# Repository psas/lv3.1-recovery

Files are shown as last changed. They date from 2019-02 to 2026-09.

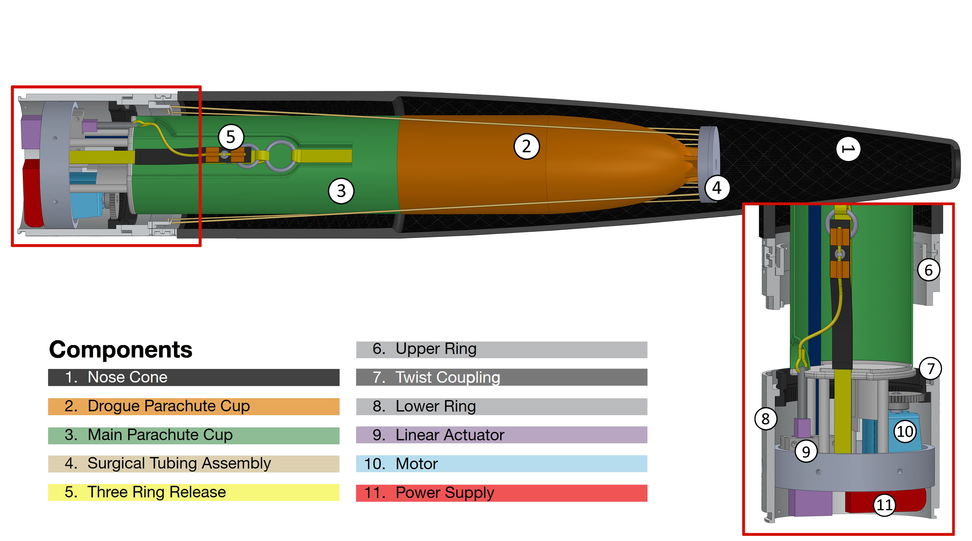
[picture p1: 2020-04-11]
images/stack_sideways.jpg

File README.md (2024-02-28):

# LV-3.1 Recovery Repository

The LV-3.1 Electromechanical Recovery System (ERS) is a fully-resettable recovery system for the [PSAS](http://psas.pdx.edu/) Launch Vehicle v 3.1 (LV-3.1). Each ERS "unit" releases a single parachute. The top unit deploys our ballute test parachute that's in the nose cone, the next ERS unit releases a standard drogue, and the final ERS unit releases the main parachute.

## Mechanical CAD
All mechanical CAD has been moved to OnShape and can be found [here](https://cad.onshape.com/documents/03e169a7501c9614bcd8fe34/w/d2206dc55680e29e4d8f6e15/e/43f9d4697ebc459acca1436a).

## Control System

In this Git repo is a PCB with STM32F091 microcontroller that controls the system. See the ControlSystem directory.

## Testing and Analysis

The ERS system will be tested by dropping it from a helicopter over a field. Many parameters must be considered for this test including wind speed, altitude, field size, parachute drag coefficients, and parachute release timing. Analysis of drop test dispersal patterns based on fixing some parameters and simulating variation in others enables us to choose an appropriate drop site and drop parameters. Analysis notebooks can by found in the /analysis directory.

* [Parent Directory](https://github.com/psas/lv3.1-recovery/tree/master/Analysis)
* [Primary mission analysis document](https://github.com/psas/lv3.1-recovery/blob/master/Analysis/Mission_Analysis.ipynb)
* [Jupyter Notebook to run simulations](https://github.com/psas/lv3.1-recovery/blob/master/Analysis/drop_test_simulator.ipynb)

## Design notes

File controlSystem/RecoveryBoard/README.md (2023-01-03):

# Electromechanical Recovery System (ERS) v4.0 Controller Board 

## General information
This board controls the ERS v4 modules in LV3.1 and hopefully eventually in LV4.

Full documentation can be found [here](https://docs.google.com/document/d/1TOoC-d3vpsw2uvtvazEmFV9_g59nFPVRWKC9Ye5qgKw/edit?usp=sharing)

## Firmware

The firmware is written in C and runs on top of ChibiOS, a small RTOS. See the "firmware" directory. The [oresat-firmware](https://github.com/oresat/oresat-firmware) repository has instructions on how to get started on the tool chain.

## License

All materials in this repo are copyright Portland State Aerospace Society and are licensed under the CERN Open Hardware Licence Version 2 -
Strongly Reciprocal (CERN-OHL-S v2), or any later version. A copy of the license is located in [here](LICENSE.md).

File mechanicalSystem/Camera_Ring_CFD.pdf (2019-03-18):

### Analysis of Drag Created by Portland State Aerospace Society’s Camera Ring Module and its Impact on Theoretical Maximum Achievable Altitudes Using Computational Fluid Dynamics in STAR CCM+

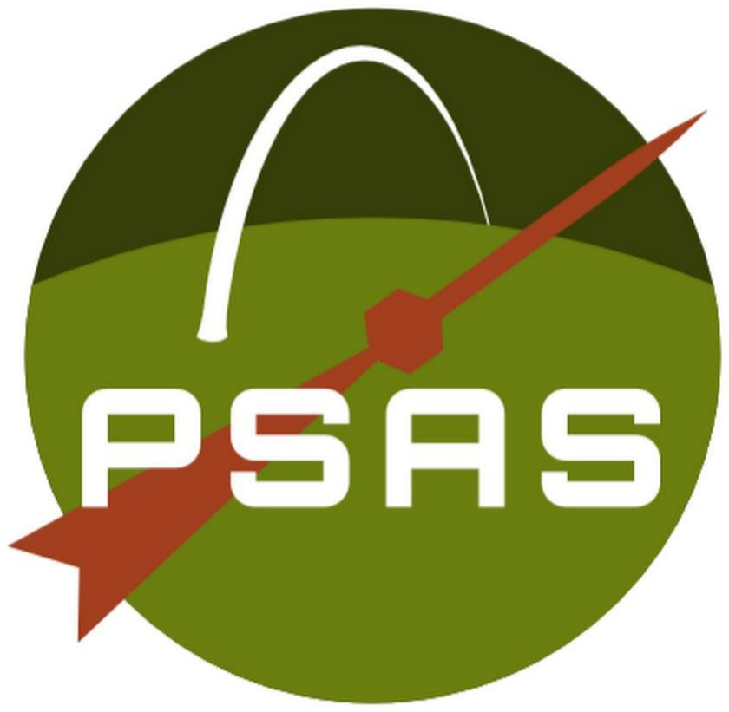
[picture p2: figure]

### 18 March 2019

### Grady Goodenough

### ME 448 Final Report

Overview

The Portland State Aerospace Society (PSAS) is constantly striving to add new improvements and features to their rockets, commonly referred to as launch vehicles, to further their reach both literally and figuratively. One of the latest components to fly aboard PSAS’ last launch vehicle, LV3, was a module comprised of 6 small cameras with wide fields of view, as shown in Figure 1. This enabled post processing of the footage into a 360° view of the launch and recovery of LV3.

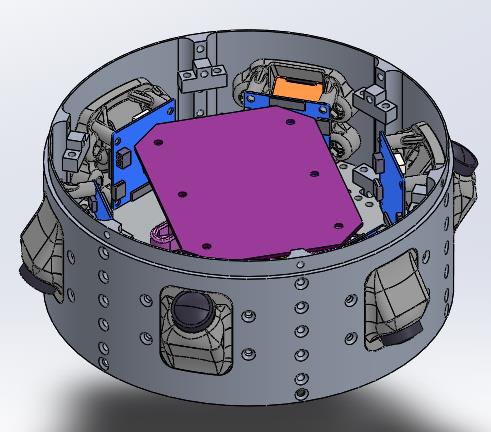
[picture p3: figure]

Figure 1: PSAS LV3 Camera Ring Module

The rocket body is comprised of a 6.6” diameter cylinder, topped with a nose cone whose curvature is prescribed by the LD-Haack Series to minimize drag. The cameras & housing protrude 0.5”, with a width of 1”.

This paper aims to explore the aerodynamic impacts of the protruding camera modules by modeling the flow over the nose cone and camera ring modules, and measuring the drag coefficient of the camera ring. The protruding features are likely to cause streamline separation and vortex shedding, which should be minimized in order to keep drag minimized and avoid any potential for tipping the rocket into unwanted spin or creating shockwaves as the rocket transitions from subsonic to supersonic speeds. A discussion of the impact of the additional drag is found in the results and discussion section.

Physical Model and Boundary Conditions

The objects of interest to this study are the camera modules protruding from the camera ring. These can be seen in Figures 2 & 3; units are in inches. For simplification, the cross sectional area was taken to be 0.5 in²
, and is used later to calculate drag coefficients for both camera orientations.

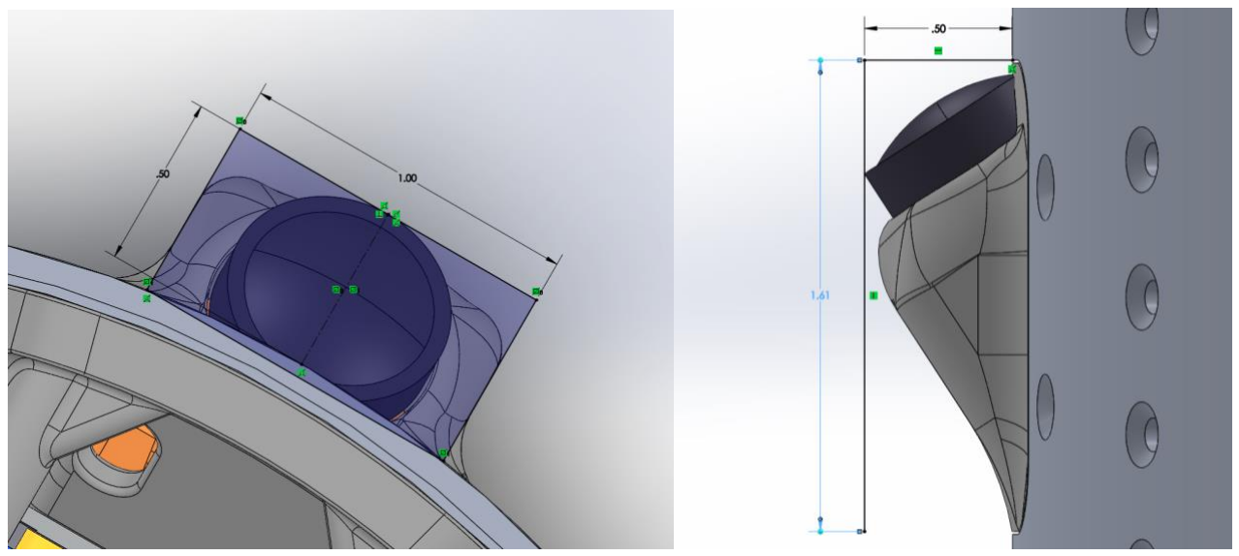
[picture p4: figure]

Figure 2: Camera module face on | Figure 3: Camera module side view

In order to save on computational power and reduce overall complexity, the simplified nose cone and camera module shown in Figure 4 were used to generate the fluid volume for STAR CCM+; units are in inches.

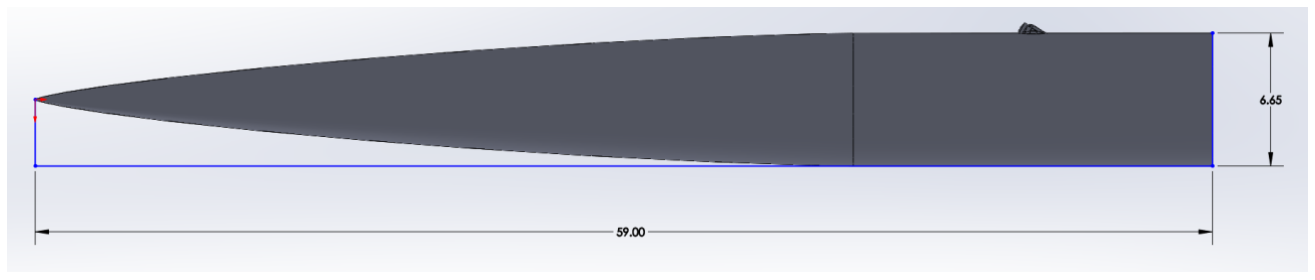
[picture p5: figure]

Figure 4: Simplified nose cone and camera module

A fluid region was created using a large cylinder and the cavity feature in Solidworks. Since the rocket is symmetrical, a 15° slice of the region was extracted and exported as a parasolid model for use with STAR CCM+, as seen in Figure 5. This region split the single camera module in half, and symmetry planes were used in STAR CCM+ to model the other half of the module. Table 1 shows the boundary conditions used.

Table 1: Boundary Conditions

Inlet Velocity | 200m/s
Constant Temperature | 300K
Initial Outlet Pressure | 0 Pa

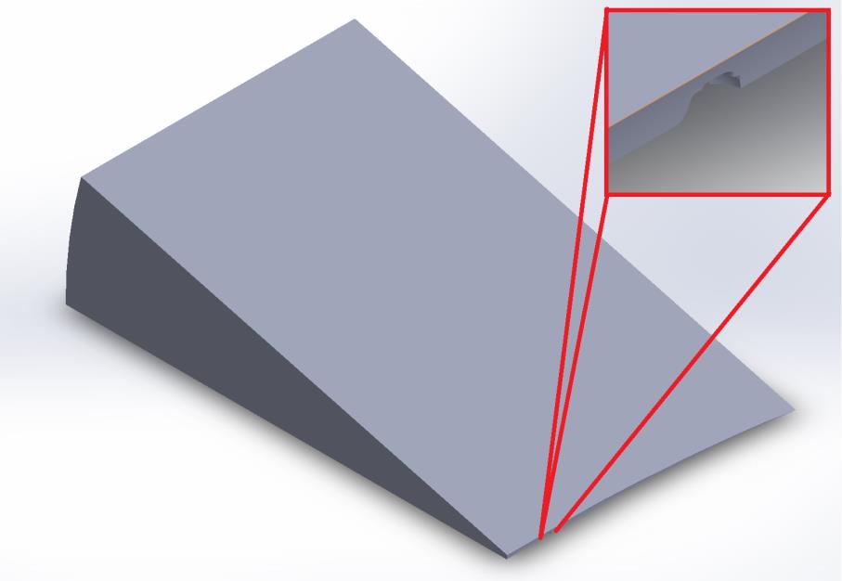
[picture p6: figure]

Figure 5: Fluid Region with breakout highlighting camera module cutout

CFD Software Features

The choices for the modeling procedure in STAR CCM+ were made to keep the model as simple as possible while allowing the flow to be visualized and the residuals to converge. A basic trimmer mesh with prism layers was applied to the fluid region, with a base size of 5cm. The nose cone and camera features, being much smaller, were modeled using independent meshes varying in size from 1-4mm. The fluid properties are the default for air, and set to behave as an ideal gas. The coupled flow solver was used and a Courant Number of 100 was used to assist in convergence. The outermost wall was set to have a slip condition to better idealize the far field state of an external flow. Grid sequencing was also used to initialize the simulation, which prevented divergence during the early iterations. The inlet was set to a velocity inlet, with a speed of 200 m/s. The outlet was set as a simple outlet. Drag coefficients were measured using the Force Coefficient report, using the boundary conditions previously described.

Three total simulations were created. One for the camera modules facing upwards, one for the camera modules facing downwards, and one for a concept cover for the cameras geared at reducing drag.

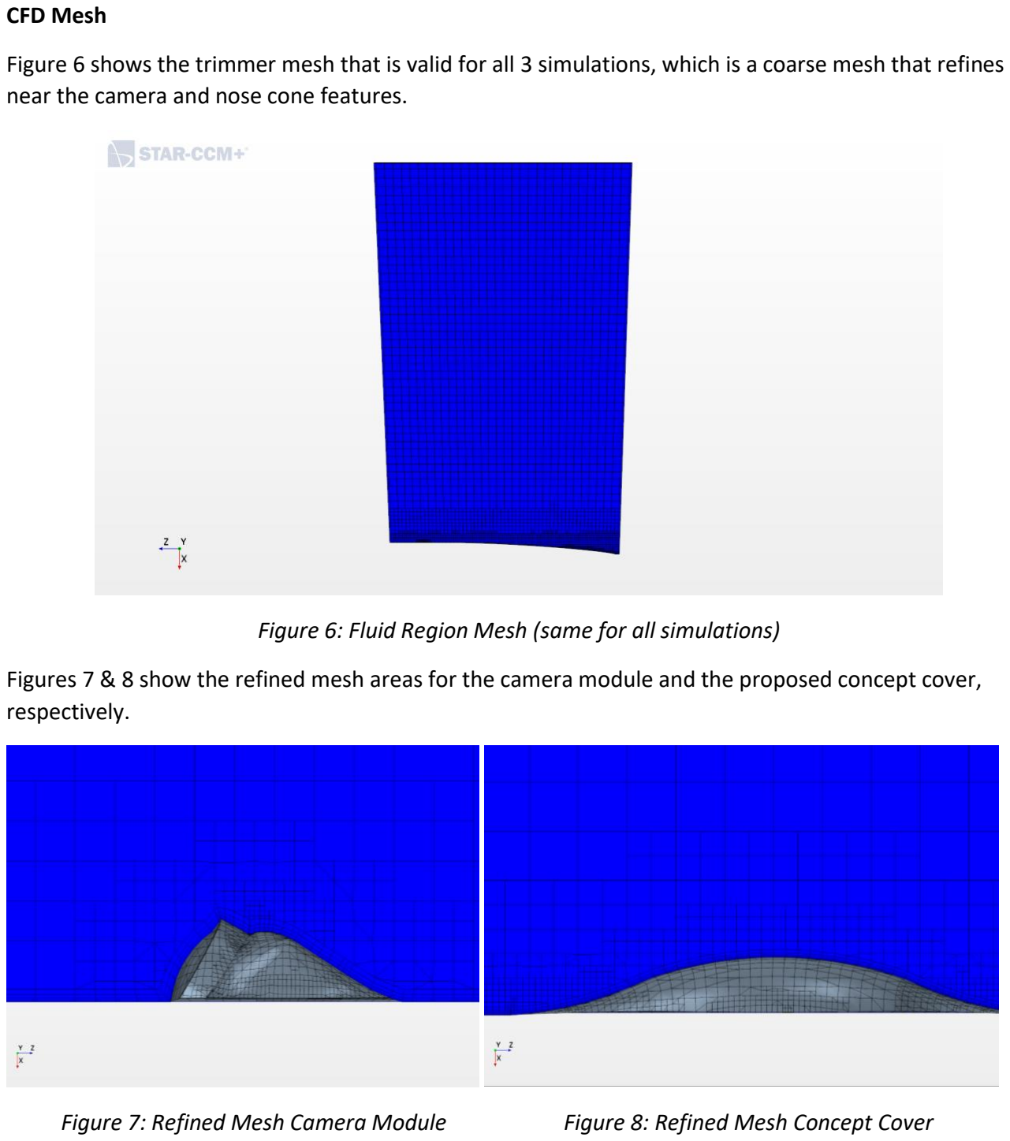
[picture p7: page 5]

CFD Mesh

Figure 6 shows the trimmer mesh that is valid for all 3 simulations, which is a coarse mesh that refines near the camera and nose cone features.

Figure 6: Fluid Region Mesh (same for all simulations)

Figures 7 & 8 show the refined mesh areas for the camera module and the proposed concept cover, respectively.

Figure 7: Refined Mesh Camera Module | Figure 8: Refined Mesh Concept Cover

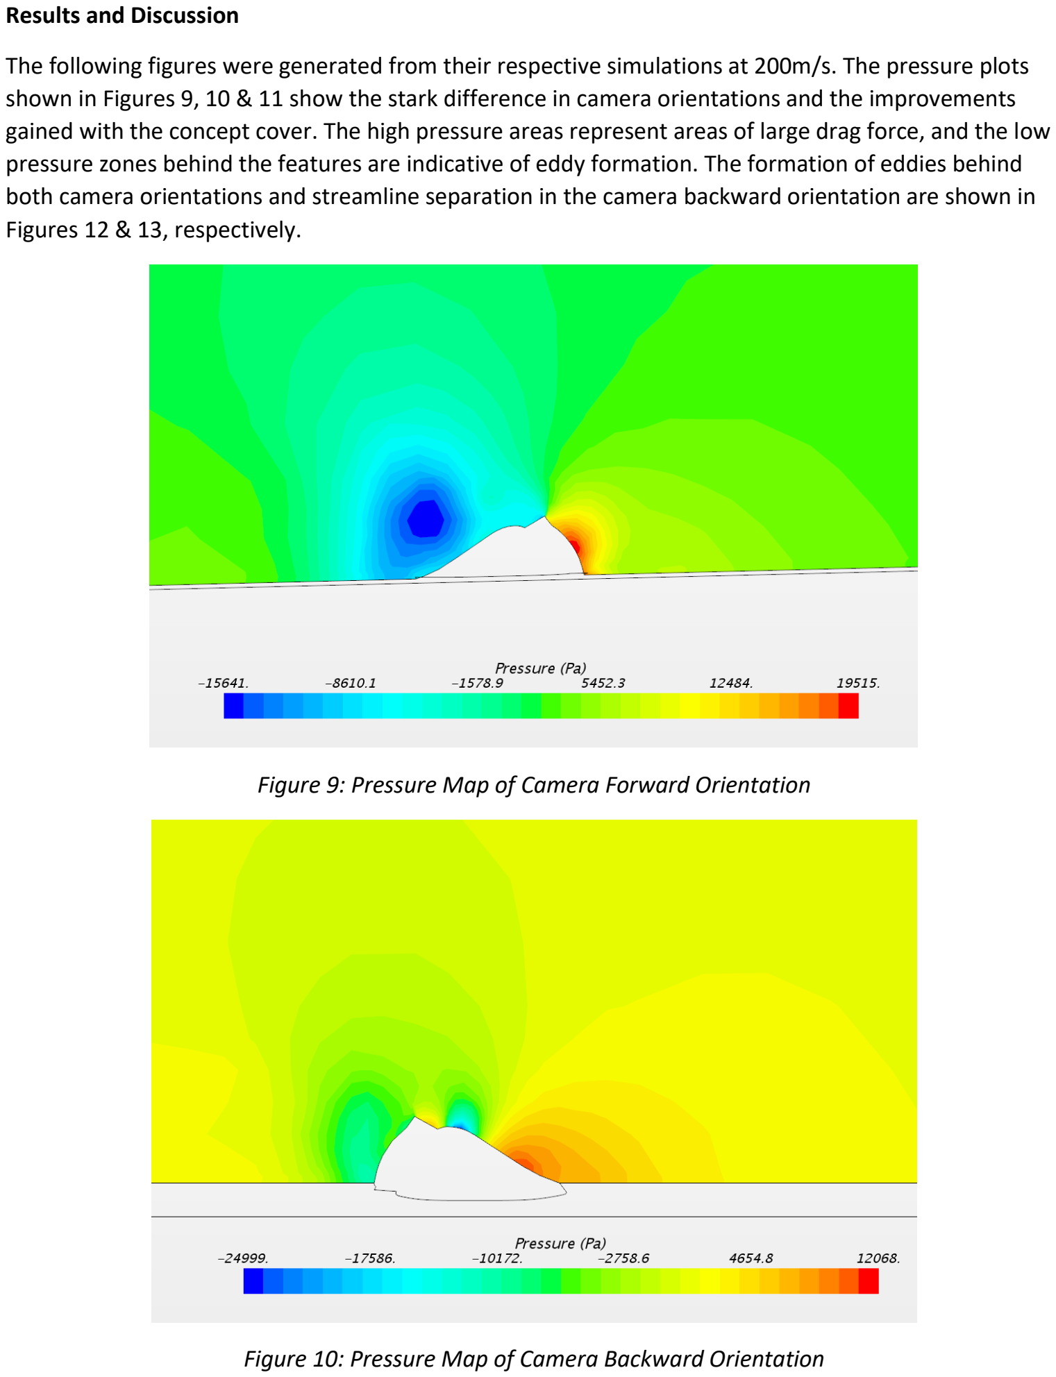
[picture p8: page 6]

Results and Discussion

The following figures were generated from their respective simulations at 200m/s. The pressure plots shown in Figures 9, 10 & 11 show the stark difference in camera orientations and the improvements gained with the concept cover. The high pressure areas represent areas of large drag force, and the low pressure zones behind the features are indicative of eddy formation. The formation of eddies behind both camera orientations and streamline separation in the camera backward orientation are shown in Figures 12 & 13, respectively.

Figure 9: Pressure Map of Camera Forward Orientation

Figure 10: Pressure Map of Camera Backward Orientation

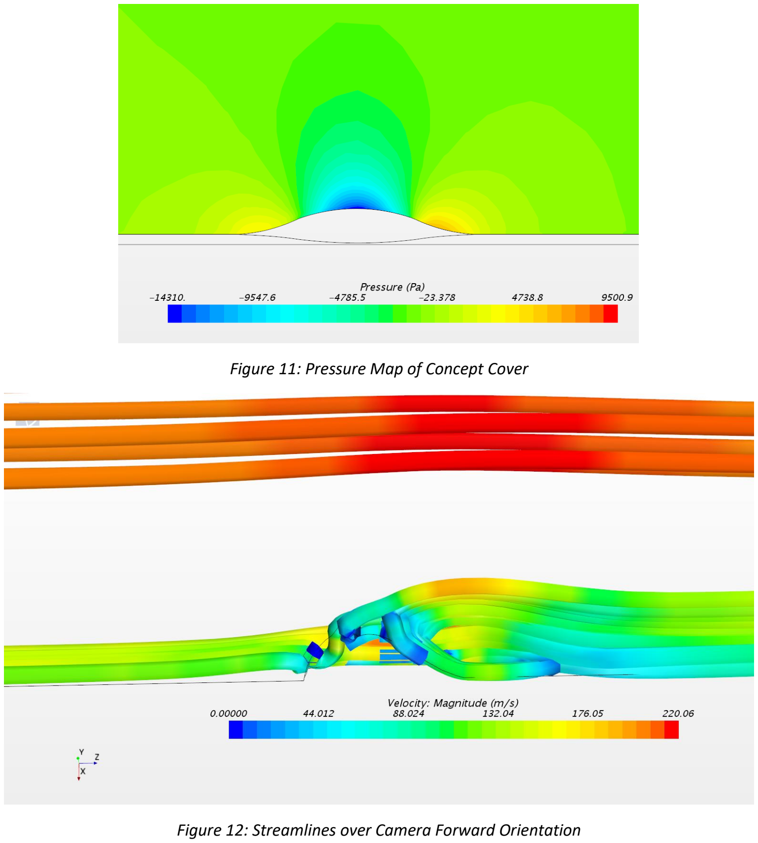
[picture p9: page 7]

Figure 11: Pressure Map of Concept Cover

Figure 12: Streamlines over Camera Forward Orientation

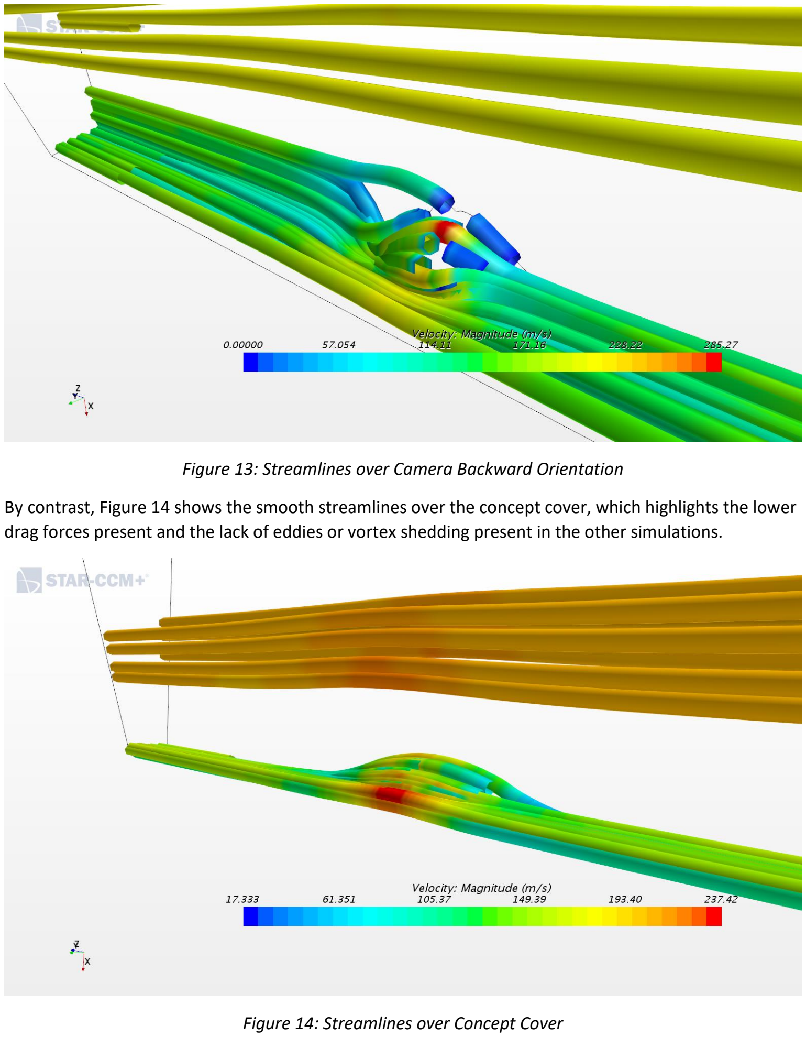
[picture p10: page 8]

Figure 13: Streamlines over Camera Backward Orientation

By contrast, Figure 14 shows the smooth streamlines over the concept cover, which highlights the lower drag forces present and the lack of eddies or vortex shedding present in the other simulations.

Figure 14: Streamlines over Concept Cover

Using the thrust (3.5kN) and burn time (6.16s) data from Pro98’s data sheets, which was used in the last LV3 launch, and the idealized equations of motion to calculate the total theoretical altitude of the rocket from Hardin’s article on rocket kinematics, and the drag coefficients generated by the STAR CCM+ simulations, the values in Table 2 were calculated. The velocities shown are a product of the drag force, and used to calculate the total altitude. The ideal case listed below matches the actual altitude reached by LV3.

Table 2: Drag Coefficients, Drag Force, and Total Theoretical Altitude

| Cd | Velocity(m/s) | Weight(N) | Fd (N) | Total Altitude (m)
Ideal | 0.00 | 299.96 | 256.27 | 0.00 | 5514.60
Camera Up | 0.33 | 260.94 | 256.27 | 35.06 | 4277.78
Camera Down | 0.18 | 277.75 | 256.27 | 18.85 | 4791.41
Both Orientations | 0.25 | 269.35 | 256.27 | 26.95 | 4534.60
Concept Cover | 0.05 | 293.09 | 256.27 | 5.55 | 5285.43

As shown in the table, there is a significant impact on the maximum altitude the rocket can achieve based on the additional drag. With the camera module in its current state, the idealize case shows a reduction in altitude of ~1000m. However, this is an idealized case, and it should be noted that the drag coefficients were calculated at 200m/s rather than the 300m/s that would satisfy the original average velocity. The decision to do so is reasonable given the linear, near constant drag coefficient values seen in Figure 15. More refinement is needed in the models to accurately represent this case, but given that there is a significant impact at 200m/s, some change to the geometry of the camera ring is warranted to improve the aerodynamic efficiencies of future launch vehicles.

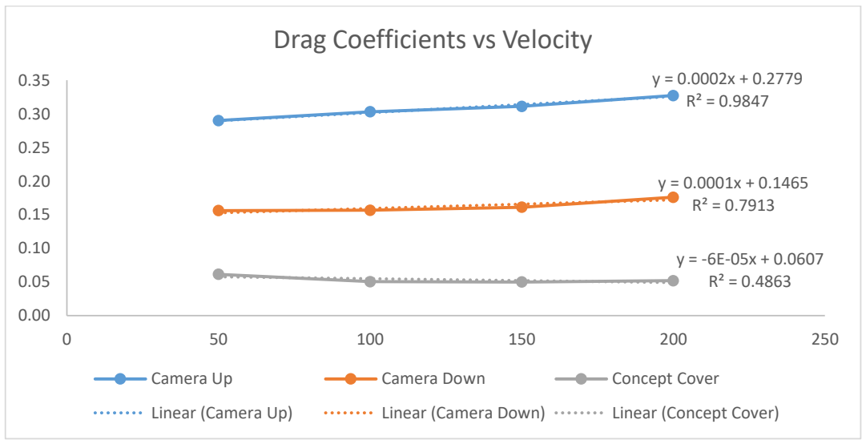
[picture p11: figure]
Drag Coefficients vs Velocity; Camera Up; Camera Down; Concept Cover; Linear (Camera Up); Linear (Camera Down); Linear (Concept Cover)

Figure 15: Plot of Cd vs Velocity over multiple runs of all simulations

The convergence plots of each simulation run at 200m/s are shown below. They show convergence after roughly 50 iterations, except for the concept simulation which was set to converge when continuity

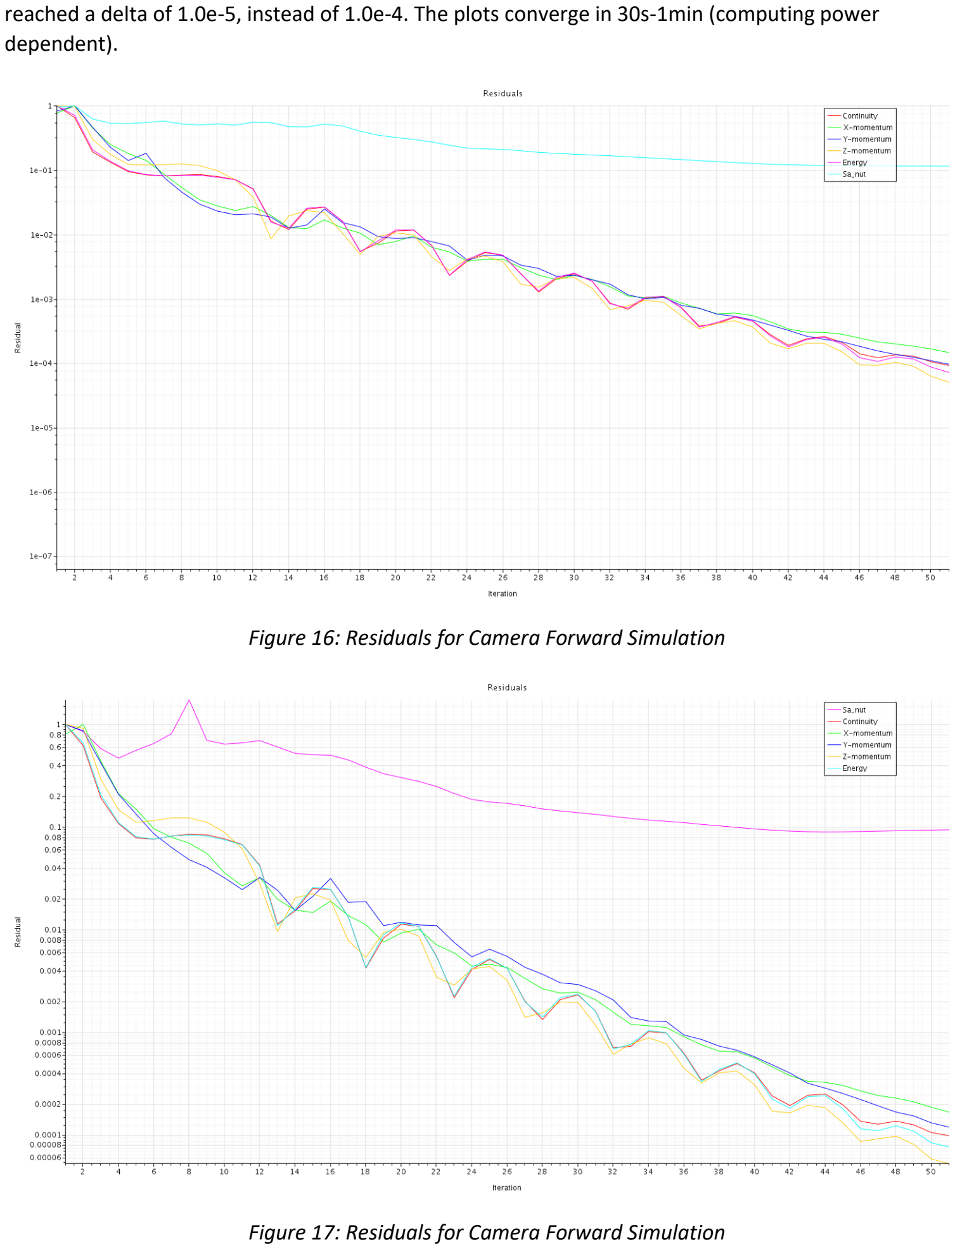
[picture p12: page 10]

reached a delta of 1.0e-5, instead of 1.0e-4. The plots converge in 30s-1min (computing power dependent).

Figure 16: Residuals for Camera Forward Simulation

Figure 17: Residuals for Camera Forward Simulation

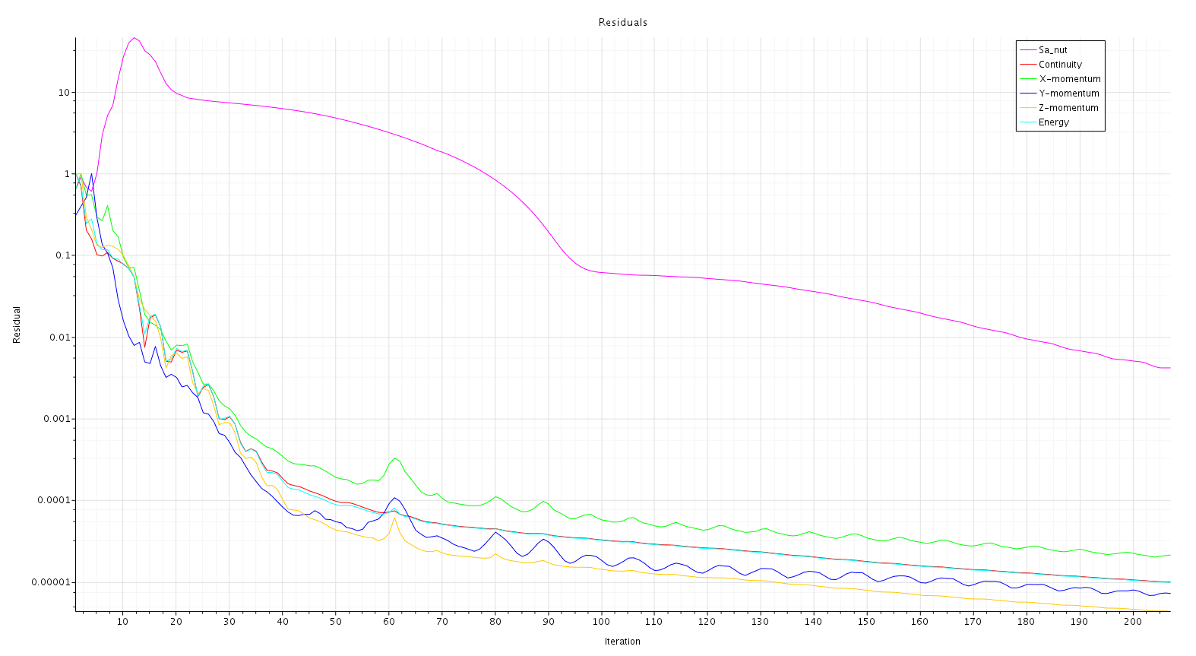
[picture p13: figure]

Figure 18: Residuals for Concept Cover Simulation

Conclusion

As demonstrated by the results in Table 2, and the visual indications of Figures 12, 13, & 14, the reduced drag produced by the concept cover is worth pursuing for PSAS’ future launch vehicles. Gaining an additional 1000m is no small feat as the organization sets its sights on reaching the Von Karman line at 100km. The conceptual cover could be made from polycarbonate or another transparent material to allow the cameras vision while creating a more aerodynamic profile. The ideal solution would be to completely encase the cameras within a uniform transparent ring, which would have to maintain a similar compressive strength to the aluminum modules. This warrants further exploration, and corrective measures may need to be taken to account for the refractive index of the material in order to not distort the field of view of the cameras.

Further expansion of these simulations can also be done to explore larger velocities, and an investigation into whether or not these features create shockwaves before the nose cone is worth pursuing as long as the current module ring remains a payload on current launch vehicles.

References

Hardin, S. (2012). How High and Fast? The Equations of Motion. Peak of Flight Newsletter,(320), 1-6. Retrieved March 18, 2019, from https://www.apogeerockets.com/education/downloads/Newsletter320.pdf.

Pro98 21062O3400-P. (n.d.). Retrieved March 18, 2019, from http://www.pro38.com/products/pro98/motor/MotorData.php?prodid=21062O3400-P

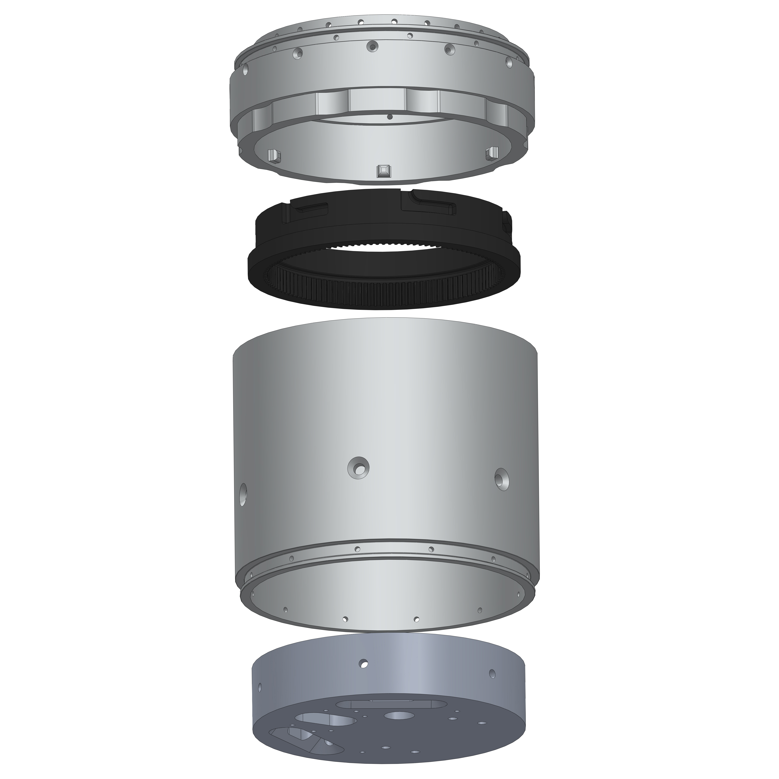
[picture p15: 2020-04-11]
images/Twist.JPG

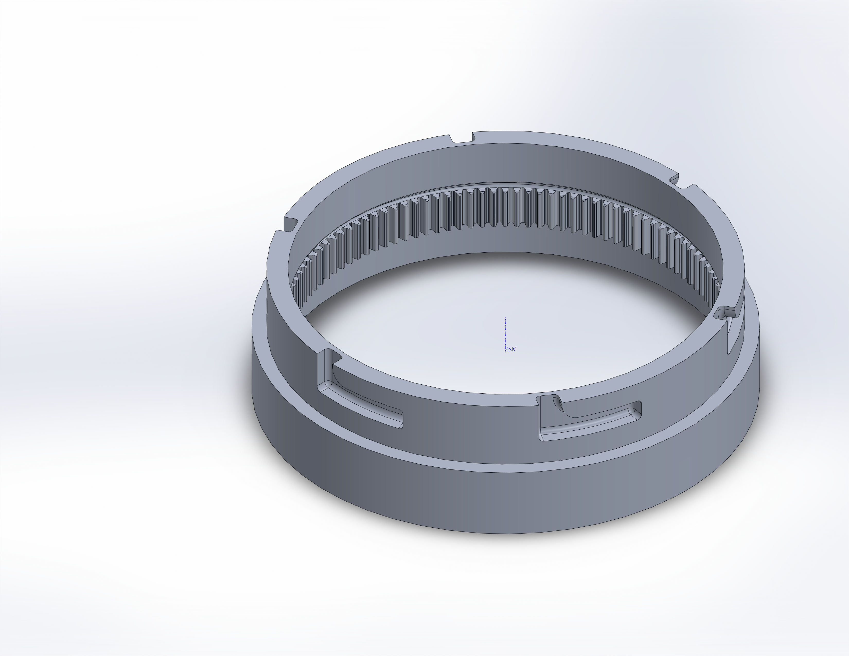
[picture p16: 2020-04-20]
images/twist_coupling_V4_skirt_teeth.PNG

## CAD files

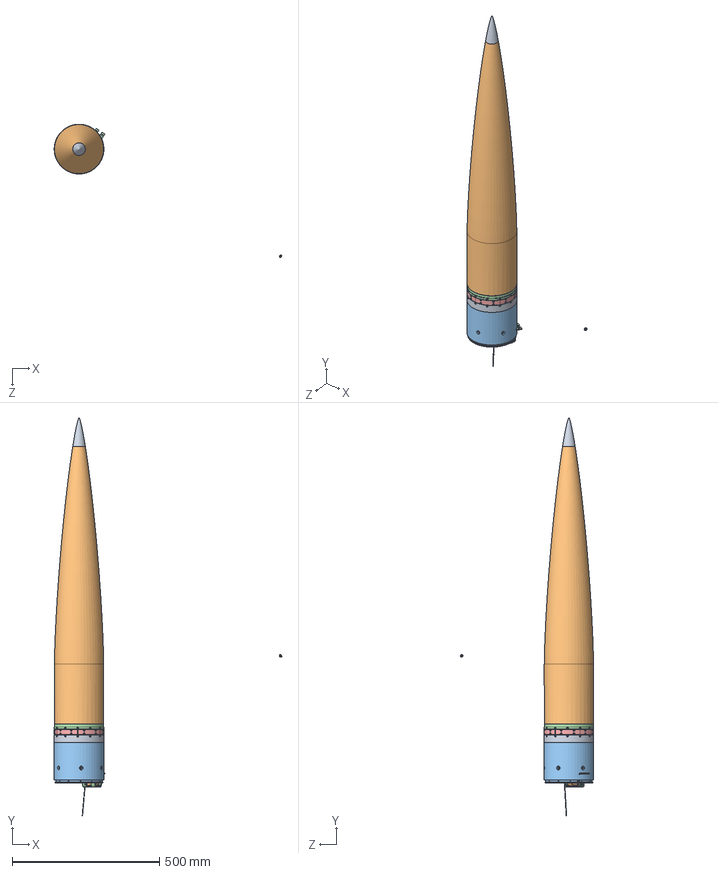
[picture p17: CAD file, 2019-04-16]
cad/Sys_architecture.SLDASM
773.4 x 1352.5 x 453.5 mm
twist_coupling_V3
keeper_ring_V3
motor_bracket_sheetmetal_V3
BLDC_Gear_Motor_100rpm
7880K450_HT-LOAD MTL GEAR--20 DEG PRESSURE ANGLE
motor_housing
ROB-12310
spindle_small
motor_brkt
95610A330_NYLON FLAT WASHER x 4
No.3_ring
No.4_ring
No.10_ring
Webbing_mid
Webbing_main
Webbing_top
grommet
yellow_cord
grommet_webbing
nylon_loop.1
main_chute_webbing
von_karmon_nose_tip2
noseconeShell
nosePlug2
moduleRing
clampArc x 6
Cup_Chute_Drogue^eNSR_v2.2
Cylinder_Chute_Main^eNSR_v2.2
8891T790_316 STAINLESS STEEL EYEBOLT
pizza_table.2

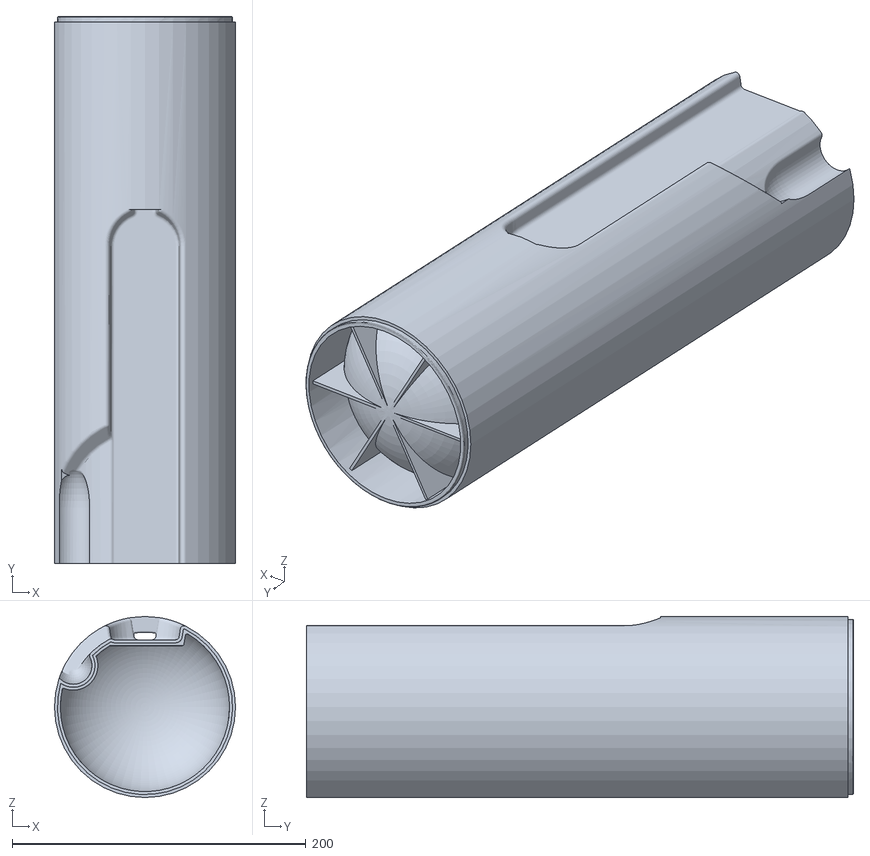
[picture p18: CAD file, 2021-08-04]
mechanicalSystem/build/mainCup.STL
123.2 x 372.1 x 123.2

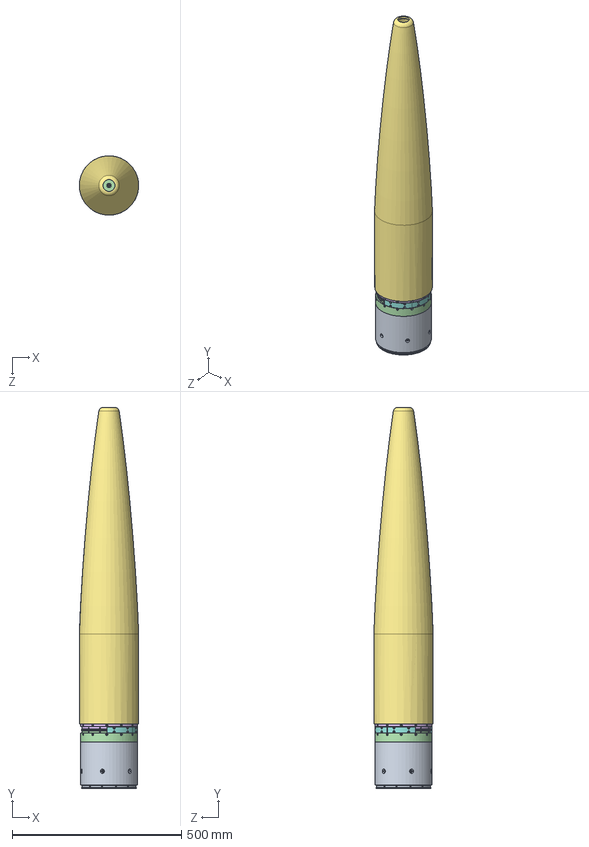
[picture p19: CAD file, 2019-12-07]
mechanicalSystem/cad/AssemblyV3.2/Assem3.2rev1.SLDASM
175.3 x 1124.8 x 175.1 mm
keeper_ring_V3
clampArc x 3
battery
H3860S_NO3_Ring
H3880S_NO4_Ring
webbing_small_V1
yellow_cord_V1.1
nylon_loop_V1
webbing_grommet_V1
grommet_V1
yellow_cord_guide x 2
H3840B_NO2_Ring
yellow_cord_short
yellow_twist
MotorHousingClamshellrev1
MotorHousingMain_rev1
BLDC_Gear_Motor_100rpm
PIZZA_v4.2
twist_coupling_V4_skirt_teeth
pcb
sensor x 2
2662N400_PLASTIC GEAR - 20 DEGREE PRESSURE ANGLE

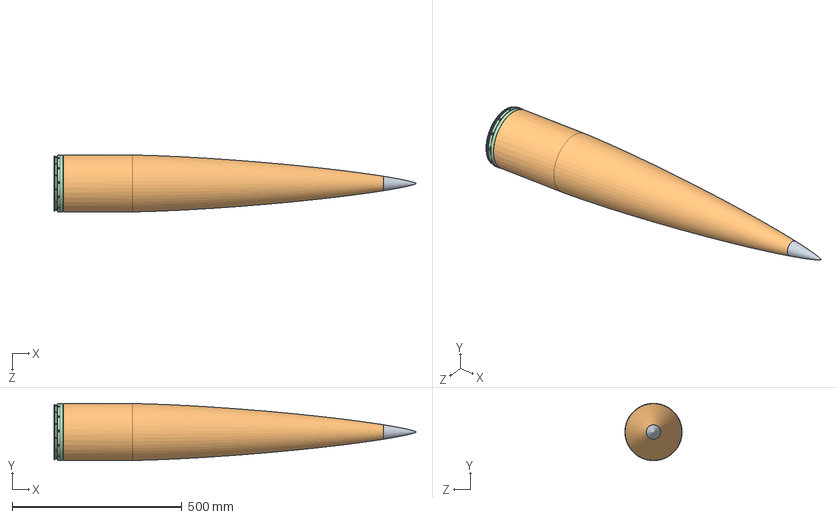
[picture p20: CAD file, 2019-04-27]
mechanicalSystem/cad/Base_11_mockup/nose.SLDASM
1067.2 x 168.9 x 168.9 mm
von_karmon_nose_tip2
noseconeShell
nosePlug2
moduleRing

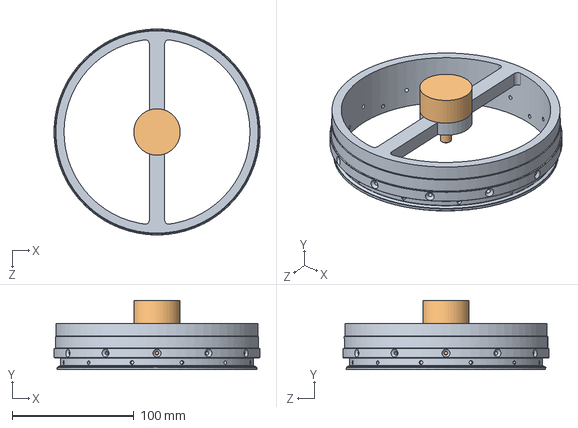
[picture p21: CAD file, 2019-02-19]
mechanicalSystem/cad/Brainstorming/GG_Concept1/Assem1.SLDASM
168.9 x 56.7 x 168.9 mm
Concept_Upper
pretend_motor

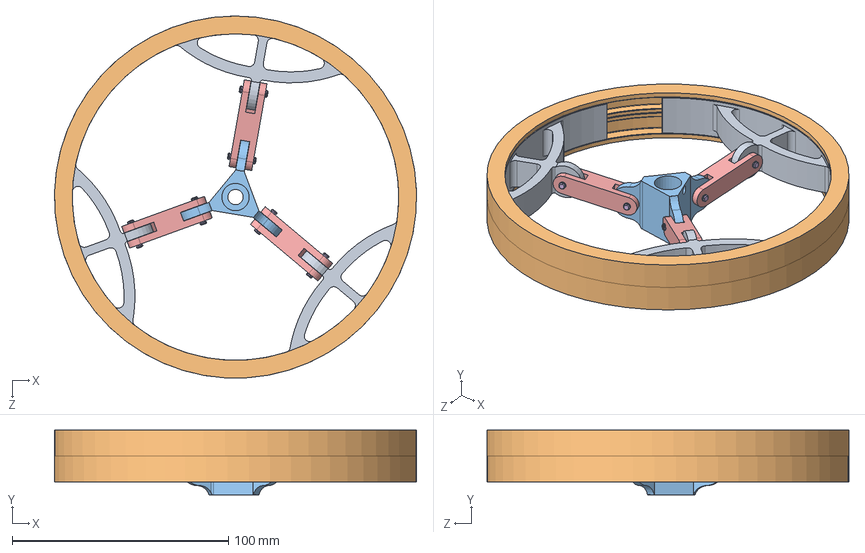
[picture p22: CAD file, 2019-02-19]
mechanicalSystem/cad/Brainstorming/GG_Concept2/Concept_Assem_2.SLDASM
167.6 x 29.9 x 167.6 mm
Clamp_Ring_Concept x 3
Ring_Concept x 2
Carriage
Bearing_RMA x 6
Linkage x 3
Dowell_Pin_1 x 6

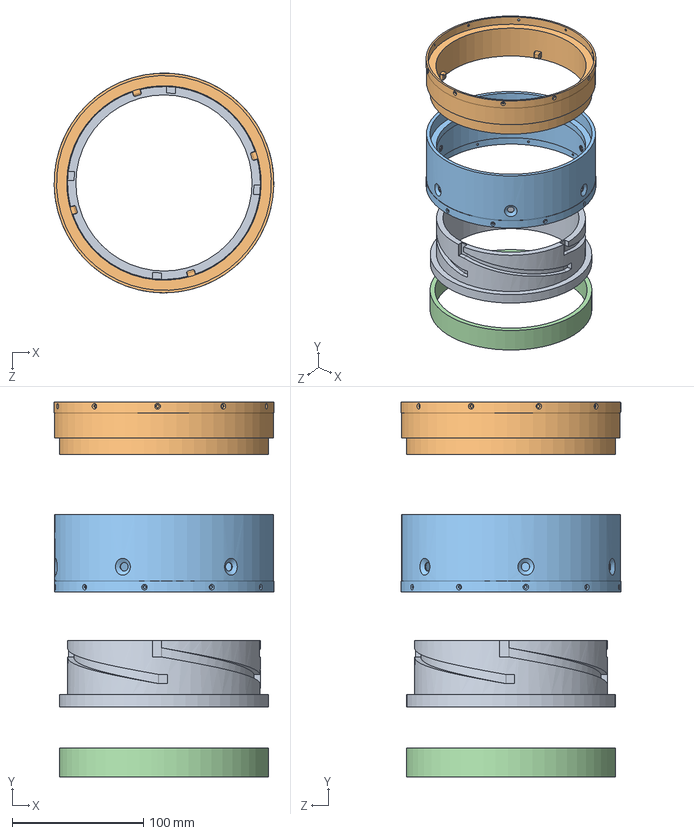
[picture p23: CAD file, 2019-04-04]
mechanicalSystem/cad/Brainstorming/GW_Concepts/proto_assemb.SLDASM
167.6 x 286.1 x 167.6 mm
twist_coupling
Bottom_ring
Top_ring
kepper ring

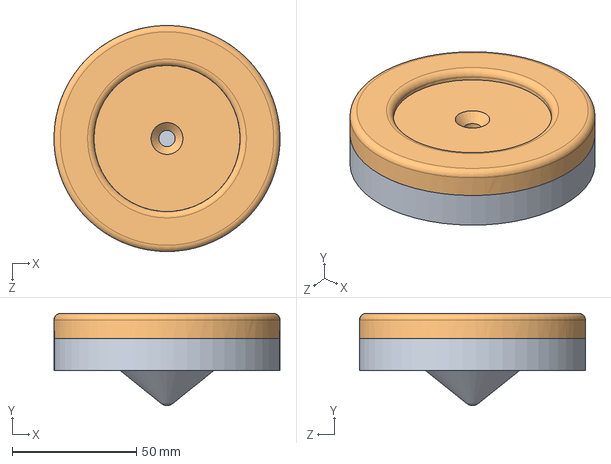
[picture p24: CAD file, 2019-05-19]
mechanicalSystem/cad/Brainstorming/ST_CAP/ST_CAP_ASSEMBLY.SLDASM
90.9 x 37.0 x 90.9 mm
ST_Bottom
ST_Cap

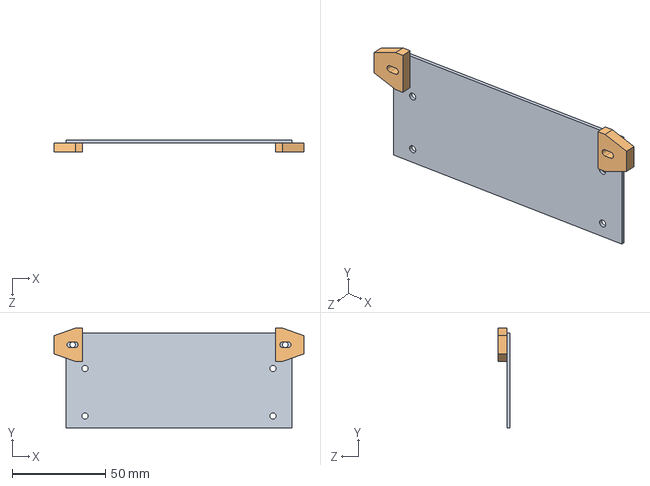
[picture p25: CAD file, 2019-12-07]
mechanicalSystem/cad/circuitboard/pcbassy.SLDASM
133.7 x 53.4 x 6.60 mm
pcb
sensor x 2

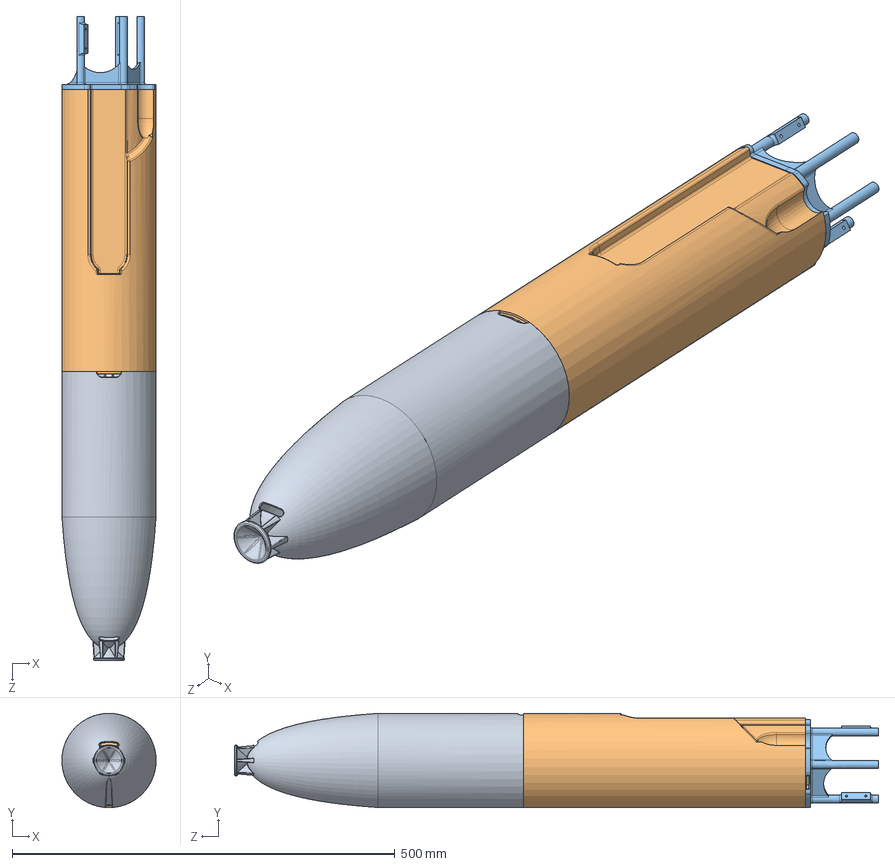
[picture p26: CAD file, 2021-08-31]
mechanicalSystem/recoverySystem.SLDASM
123.2 x 123.2 x 841.4 mm
drougeCup
mainCup
mainPlug

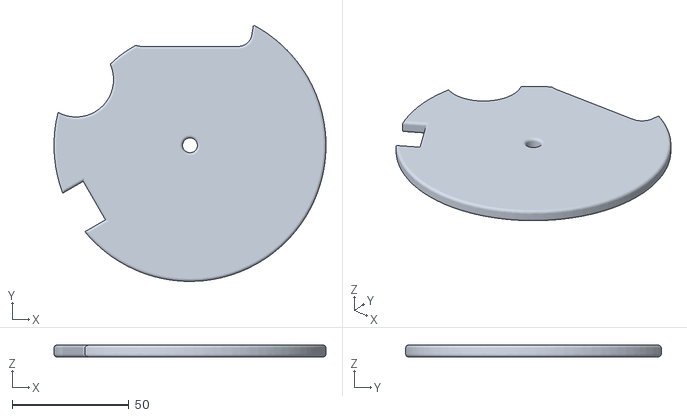
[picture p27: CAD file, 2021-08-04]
mechanicalSystem/build/mainPlug.STL
116.6 x 109.6 x 5.08

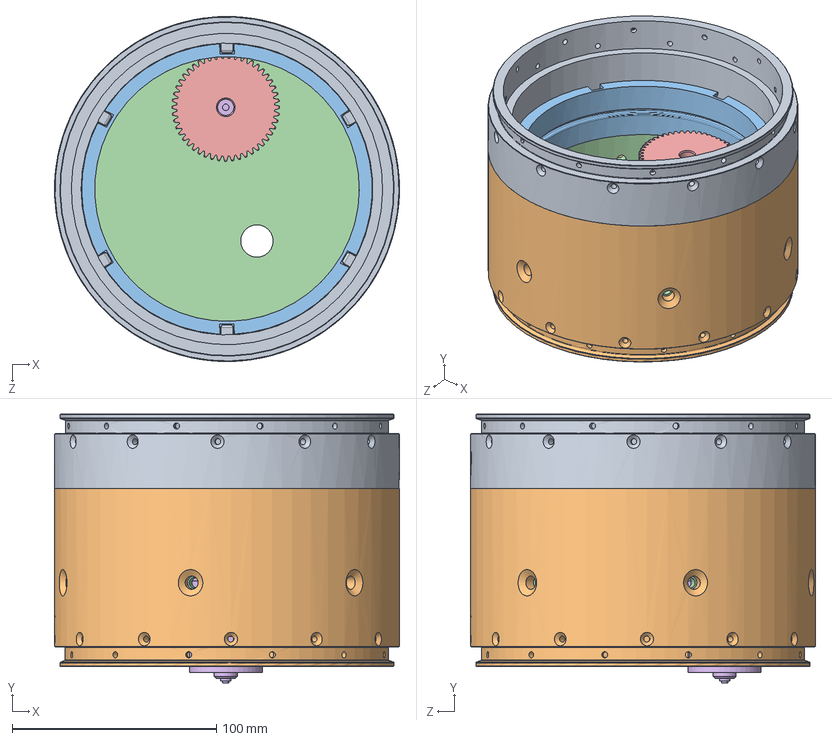
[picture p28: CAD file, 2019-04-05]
mechanicalSystem/cad/Base_11_mockup/Base11_NCSR.SLDASM
168.9 x 131.6 x 168.9 mm
Bottom_ring
Top_ring
twist_coupling
kepper ring - Base 11
7880K450_HT-LOAD MTL GEAR--20 DEG PRESSURE ANGLE
Motor1_small

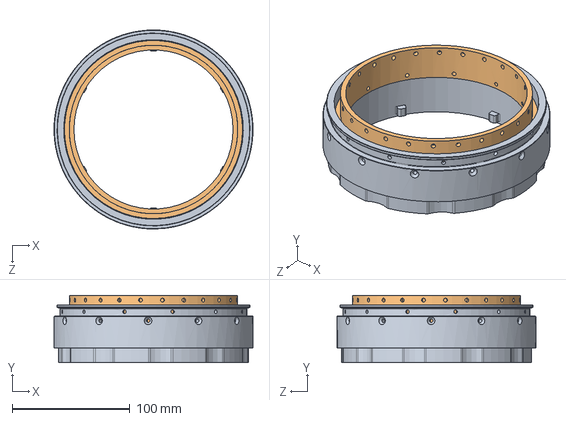
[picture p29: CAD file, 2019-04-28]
mechanicalSystem/cad/Brainstorming/GG_Full_Mockup/upper_ring_assy.SLDASM
168.9 x 57.2 x 168.9 mm
upper_ring_V3
tube_ring_V3

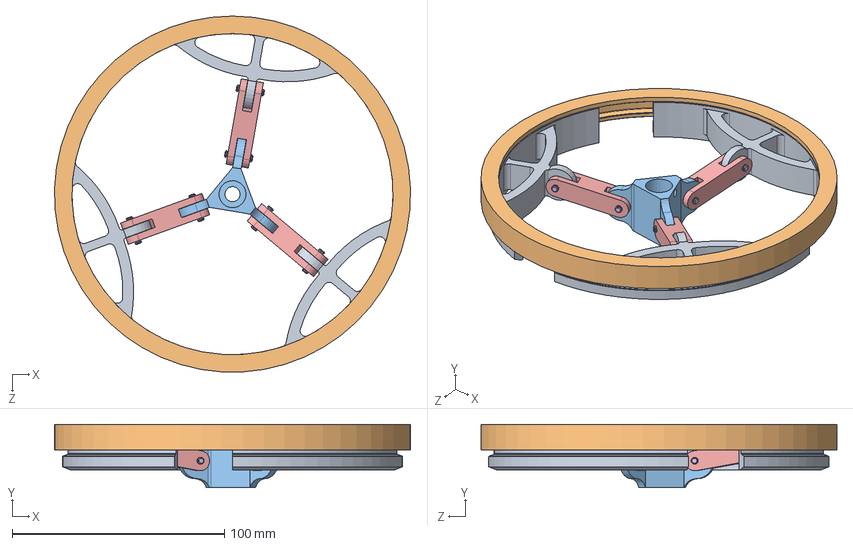
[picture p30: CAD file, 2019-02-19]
mechanicalSystem/cad/Brainstorming/GG_WIP/Upper_Ring_Carriage_Clamps.SLDASM
167.6 x 29.9 x 167.5 mm
Clamp_Ring_Concept x 3
Ring_Concept
Carriage
Bearing_RMA x 6
Linkage x 3
Dowell_Pin_1 x 6

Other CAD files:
mechanicalSystem/parachuteCups/mainCup.SLDPRT
mechanicalSystem/cad/Brainstorming/MH_Concepts/DCR_Concept2/Thesis1_assy.SLDASM
mechanicalSystem/cad/Brainstorming/MH_Concepts/SMA_Protos/Proto1.SLDASM
mechanicalSystem/cad/Parachute_Cups/ERS_Parachute_System/Assem_Parachute_Cups.SLDASM
Current_Ring/Bottom_ring.SLDDRW
Current_Ring/Bottom_ring.SLDPRT
Current_Ring/Bottom_ring_1.SLDPRT
Current_Ring/Bottom_ring_2.SLDPRT
Current_Ring/Old/Bottom_ring.SLDPRT
Current_Ring/Top_ring.SLDDRW
capstoneArchive/Nose_cone/Nose_cone_bot.SLDPRT
capstoneArchive/Nose_cone/Nose_cone_bot.STL
capstoneArchive/Nose_cone/Nose_cone_mid.SLDPRT
capstoneArchive/Nose_cone/Nose_cone_mid.STL
capstoneArchive/Nose_cone/Nose_cone_top.1.SLDPRT
capstoneArchive/Nose_cone/Nose_cone_top.1.STL
capstoneArchive/Nose_cone/Nose_cone_top.2.SLDPRT
capstoneArchive/Nose_cone/Nose_cone_top.2.STL
capstoneArchive/Nose_cone/Nose_cone_top.SLDPRT
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

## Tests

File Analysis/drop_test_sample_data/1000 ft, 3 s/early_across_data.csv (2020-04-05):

 | x | y | norm | theta | v_plane | v_w | deg_w | mode
0 | 29.84554108934917 | 529.844887222333 | 530.6848036627417 | 1.5145269623795692 | 29.981671507452063 | 3.5410881635839644 | 85.1753187704822 | early
1 | -90.85455929829655 | 753.5643067277181 | 759.021551287784 | 1.6907836059249064 | 31.194199211870753 | 4.957456167171788 | 89.90883739045869 | early
2 | -49.430339060058394 | 488.6965767112853 | 491.19008795874686 | 1.6716007899782424 | 27.236441925133256 | 3.308997522414632 | 85.23878303554459 | early
3 | -114.99912416840009 | 998.8090909663252 | 1005.4075784260212 | 1.6854278141711447 | 27.74271200736993 | 6.961376861153502 | 97.46764593749326 | early
4 | 5.951564218096907 | 378.53715046823606 | 378.58393442043223 | 1.5550750854894633 | 33.03212693306156 | 2.305326214136373 | 77.34994694914315 | early
5 | -53.191733401657466 | 239.1109949254655 | 244.95597236344125 | 1.7896882688943343 | 29.284223918636528 | 1.6899988814787459 | 94.99020827195643 | early
6 | -148.06886824870983 | 642.6426126974 | 659.4800356333724 | 1.7972505104329581 | 33.14535169231281 | 4.696582059376601 | 99.48570690020364 | early
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

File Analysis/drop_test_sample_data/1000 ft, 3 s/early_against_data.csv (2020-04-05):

 | x | y | norm | theta | v_plane | v_w | deg_w | mode
0 | 1000.7225768369594 | 242.79598660669646 | 1029.7551004503564 | 0.23802144778429185 | 17.060110876831956 | 7.433723066013281 | 12.989378159047211 | early
1 | 2109.062025582899 | 163.94482219922602 | 2115.4244331768928 | 0.07757752025522549 | 5.428362623747764 | 14.836412975918757 | 3.374756941905014 | early
2 | 901.2674157442461 | -28.496439107208467 | 901.7178060369567 | -0.03160765411819628 | 19.012670587721246 | 6.092368445820827 | 0.2249053023338848 | early
3 | 1041.1854246880305 | 46.20477974326505 | 1042.2101372822651 | 0.04434799381200677 | 12.37477513199625 | 7.216805654333403 | 2.034237287286793 | early
4 | 851.8297264440424 | -109.07484042197845 | 858.7847248681197 | -0.12735467631894656 | 14.279633316615952 | 6.092752961925353 | -8.986469594155091 | early
5 | 781.2537650030235 | -78.33663193138132 | 785.171365520771 | -0.09993637368210112 | 17.035867631187386 | 5.647892176285248 | -4.181963001565762 | early
6 | 1797.134902972002 | -200.19380124109142 | 1808.2509277021109 | -0.11093871581457795 | 14.996817441706664 | 13.073026299547127 | -5.106525906940494 | early
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

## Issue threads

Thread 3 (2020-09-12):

Eagle Polarity Markers

davidalay, 2020-09-12:
The polarity markers on all diodes should be moved to not be underneath the footprint of the part.  This is so they are not obscured by solder paste during assembly.  Additionally U$5 needs a polarity marker.

Closed 2025-04-23.

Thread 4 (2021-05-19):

Triggering the speaker browns out the board.

andrewgreenberg, 2021-05-19:
It really shouldn't brown out with a 17 ohm speaker, but :shrug:

Consider: adding bulk capacitor, adding resistor, etc.

Closed 2025-04-23.

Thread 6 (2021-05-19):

Changes for v3

andrewgreenberg, 2021-05-19:
- Upgrade to F091 processor
- Add OreSat debug connector
- Better power layout (swap battery charger / 3.3V supply)
- Arm switch is slow to kill uC; why? (symptom: lots of garbage on serial port as the uC browns out)
- Switch out to better polarized, locking connectors (2 mm?)
- Fuses or other current limiting on motors so they can't die horribly

andrewgreenberg, 2025-04-23:
Oh wow this is an old issue; v3 fixes all of this.

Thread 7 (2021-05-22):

Telemetrum interface is wrong

andrewgreenberg, 2021-05-22:
1. The telemetrum provides a common `v_lipo` and then pulls the `apogee` and `main` lines to ground using an N channel MOSFET. The current v2 recovery board is designed for a common ground and the two lines going high. This MUST be fixed.
1. The Telemetrum constantly checks for a low value resistance between `v_lipo` and the `apogee` and `main` lines. If this voltage falls below 3.2V, then the Telemetrum won't ever arm. In order to "spoof" the Telemetrum into thinking a valid igniter is attached, a resistor should be put across the optoisolator's LED to prevent the LED's forward voltage (1.3 - 1.75V) from triggering the "bad ignitor" levels. This should be tested, but even a high resistance like 1k should do the trick since the Telemetrum uses a 100k / 27k voltage divider to measure that voltage.

andrewgreenberg, 2025-04-23:
This was a v2 issue; fixed in v3?

Closed 2025-04-23.

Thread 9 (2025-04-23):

UART RX into uC needs 1k resistor or more to stop back powering

andrewgreenberg, 2025-04-23:
When the RBF plug is in, and the ERS should be powered off, the UART can back power it if plugged in.

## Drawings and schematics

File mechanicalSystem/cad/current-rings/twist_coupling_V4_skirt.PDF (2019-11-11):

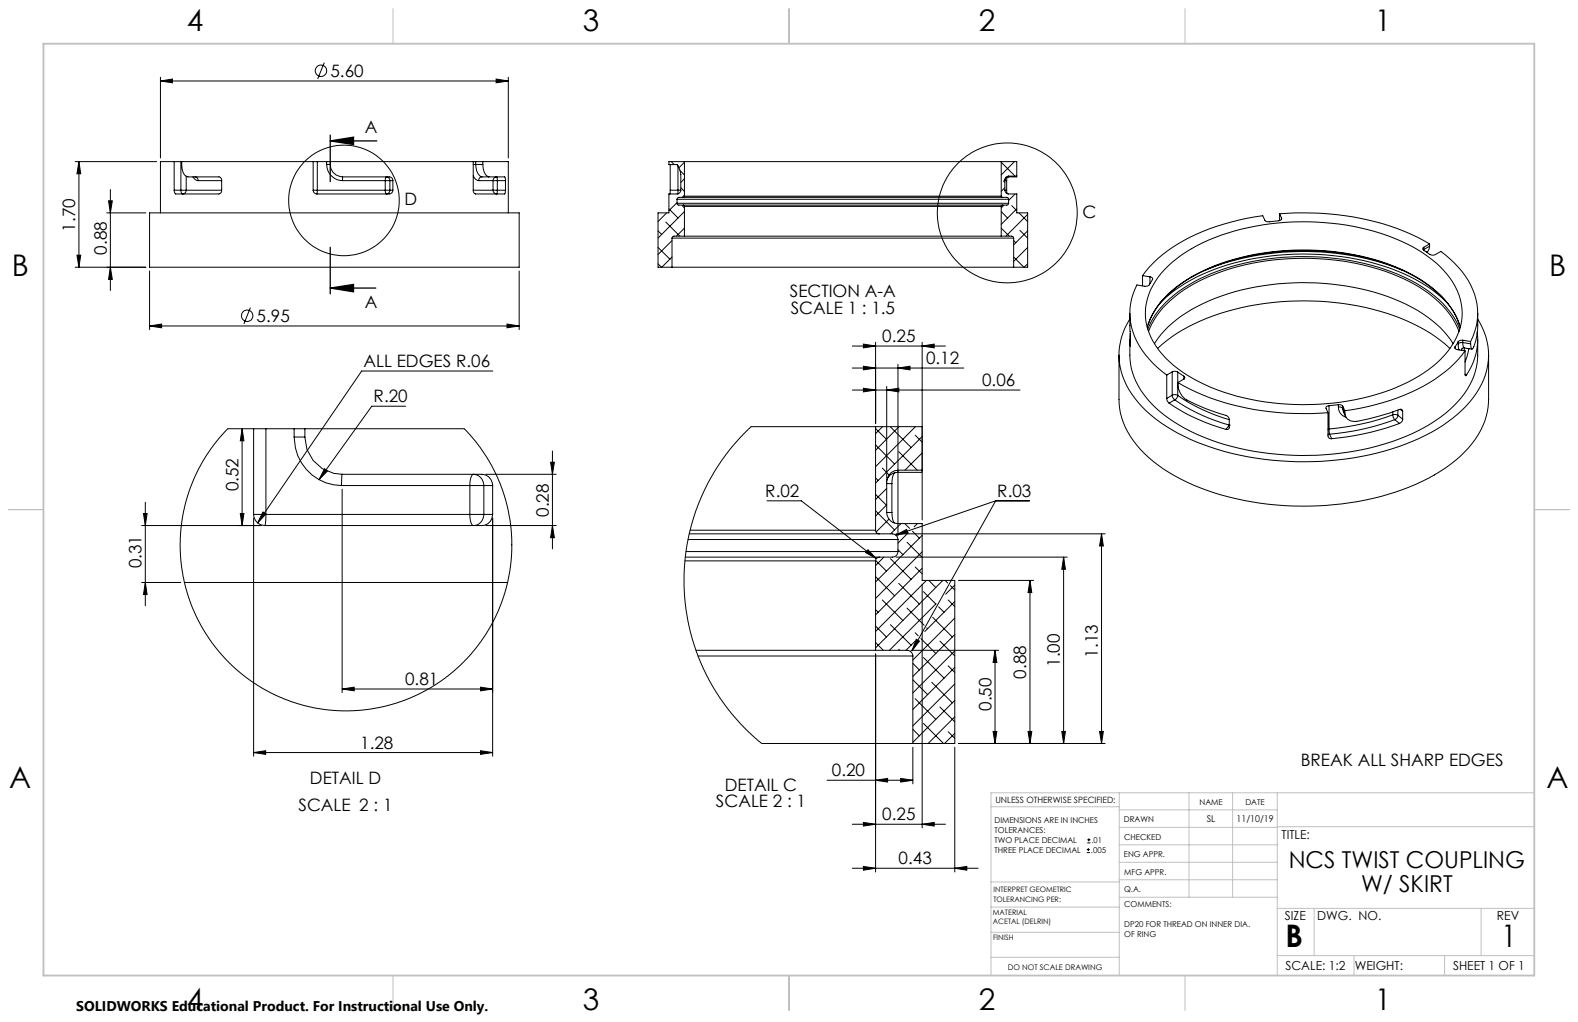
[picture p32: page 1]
DETAIL D SCALE 2 : 1; ALL EDGES R.06; SECTION A-A SCALE 1 : 1.5; DETAIL C SCALE 2 : 1; DO NOT SCALE DRAWING; SHEET 1 OF 1; SCALE: 1:2; WEIGHT:; DWG. NO.; REV; ACETAL (DELRIN)

BREAK ALL SHARP EDGES

UNLESS OTHERWISE SPECIFIED: | | NAME | DATE
DIMENSIONS ARE IN INCHES TOLERANCES: TWO PLACE DECIMAL .01 THREE PLACE DECIMAL .005 | DRAWN | SL | 11/10/19

CHECKED | | | TITLE: NCS TWIST COUPLING W/ SKIRT

ENG APPR.
MFG APPR.

INTERPRET GEOMETRIC TOLERANCING PER: | Q.A.

COMMENTS:
DP20 FOR THREAD ON INNER DIA.
OF RING

SOLIDWORKS Educational Product. For Instructional Use Only.

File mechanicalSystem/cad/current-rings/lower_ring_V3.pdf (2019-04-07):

5.63 | .50

.25

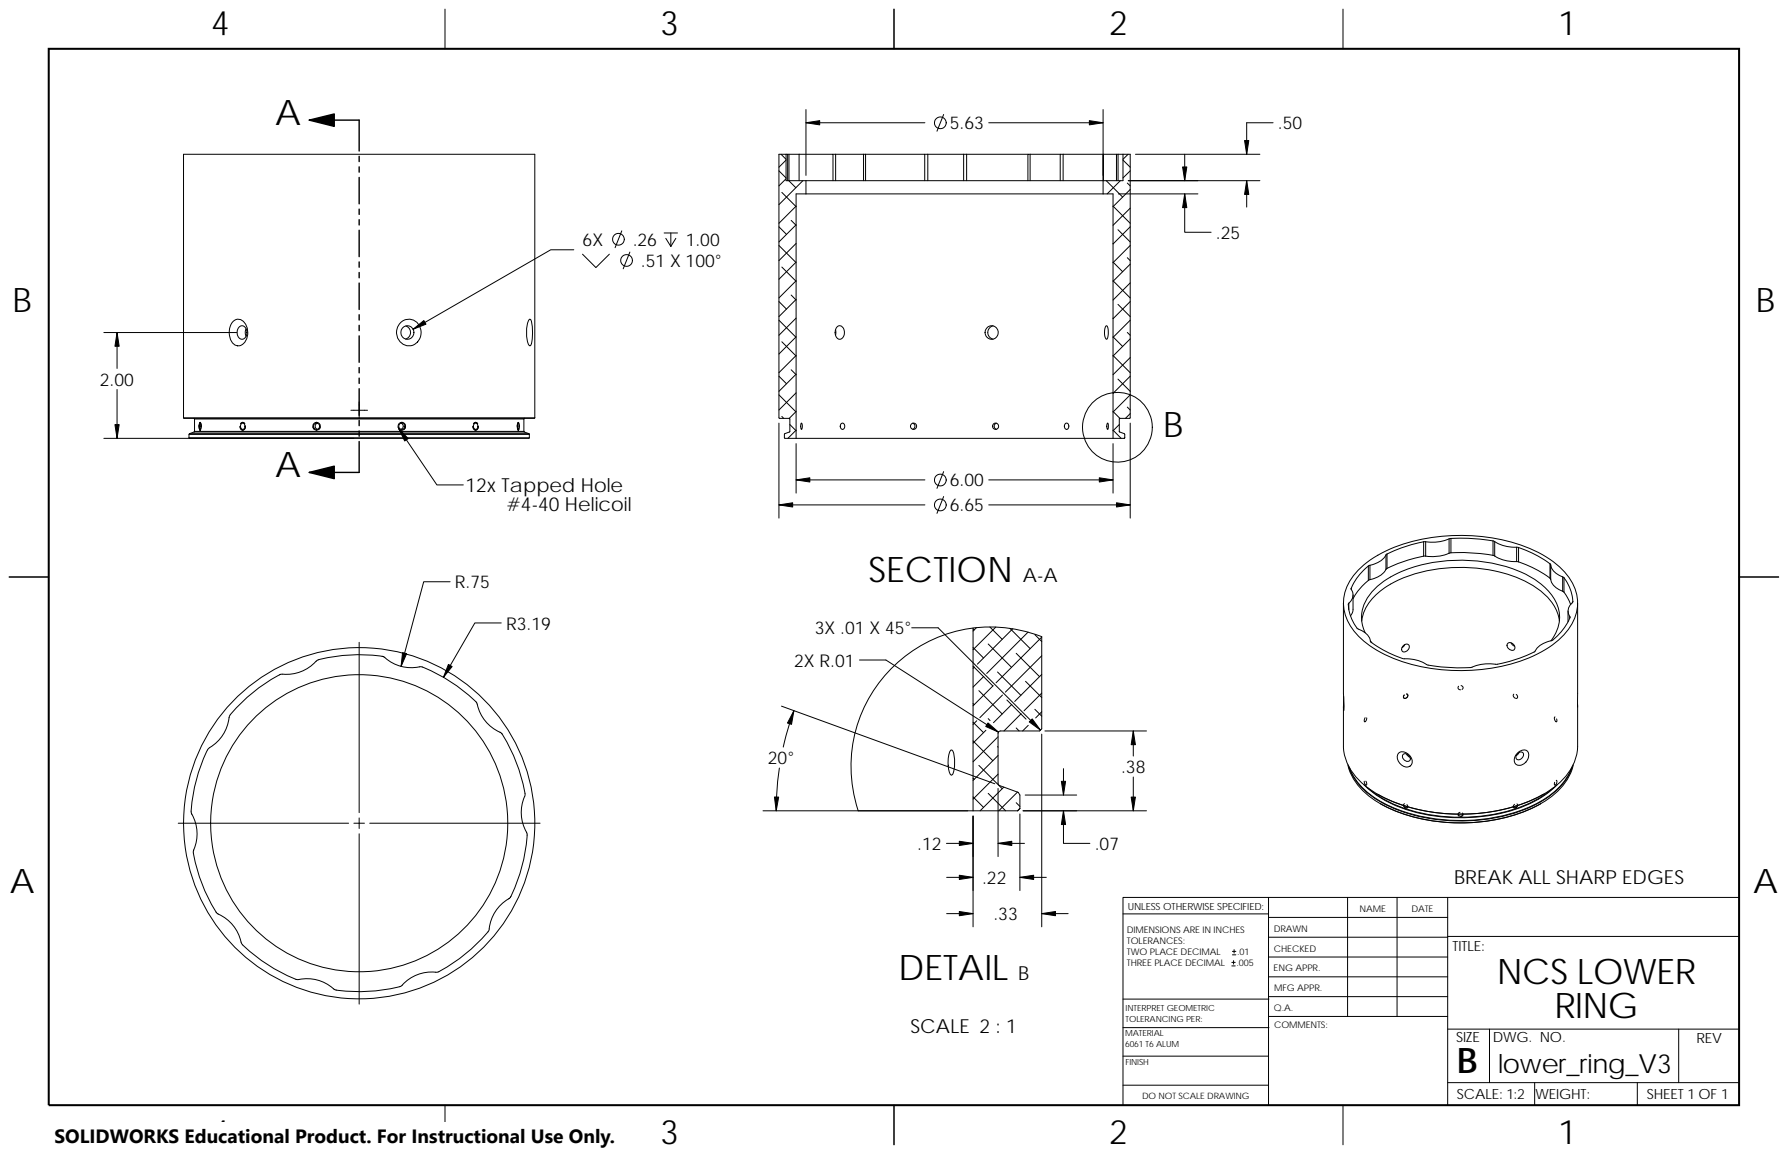
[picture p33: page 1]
SECTION A-A; DETAIL B; SCALE 2 : 1; 12x Tapped Hole #4-40 Helicoil; SHEET 1 OF 1; INTERPRET GEOMETRIC; MATERIAL; TOLERANCING PER:; 6061 T6 ALUM; RING; lower_ring_V3; REV; DO NOT SCALE DRAWING; SCALE: 1:2; WEIGHT:; DWG. NO.; SIZE; TITLE:; NAME; DATE; COMMENTS:; DRAWN; NCS LOWER; FINISH; TWO PLACE DECIMAL

BREAK ALL SHARP EDGES

UNLESS OTHERWISE SPECIFIED:

DIMENSIONS ARE IN INCHES
TOLERANCES:
THREE PLACE DECIMAL .005

CHECKED
ENG APPR.
MFG APPR.
Q.A.

SOLIDWORKS Educational Product. For Instructional Use Only.

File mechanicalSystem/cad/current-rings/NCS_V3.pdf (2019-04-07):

1

2

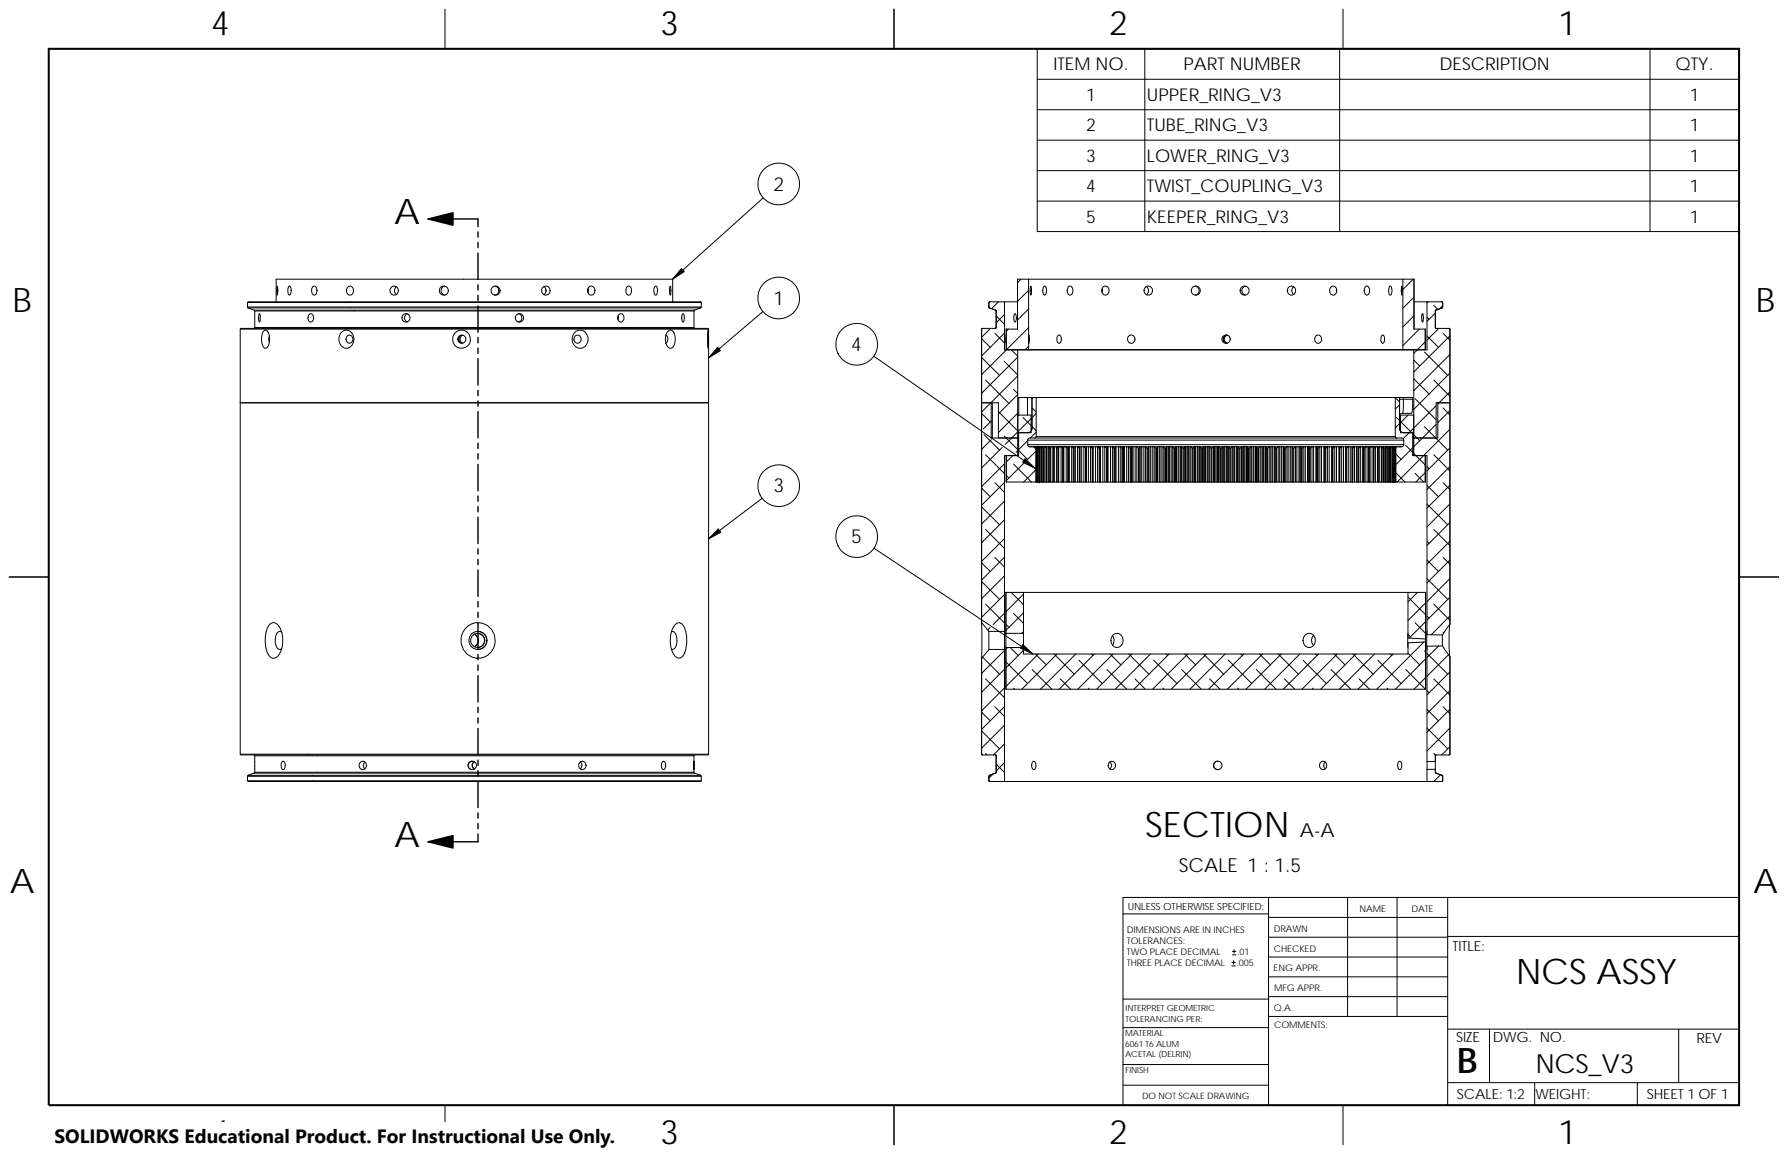
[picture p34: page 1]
SCALE 1 : 1.5; SECTION A-A; ITEM NO.; PART NUMBER; DESCRIPTION; QTY.; UPPER_RING_V3; TUBE_RING_V3; LOWER_RING_V3; TWIST_COUPLING_V3; KEEPER_RING_V3; DWG. NO.; TITLE:; DATE; COMMENTS:; SHEET 1 OF 1; FINISH; MATERIAL; SCALE: 1:2; SIZE; NCS ASSY; NAME; WEIGHT: 1; NCS_V3; 6061 T6 ALUM; REV; ACETAL (DELRIN); INTERPRET GEOMETRIC TOLERANCING PER:; TWO PLACE DECIMAL

UNLESS OTHERWISE SPECIFIED:

DIMENSIONS ARE IN INCHES
TOLERANCES:
THREE PLACE DECIMAL .005

DRAWN
CHECKED
ENG APPR.
MFG APPR.
Q.A.

DO NOT SCALE DRAWING

SOLIDWORKS Educational Product. For Instructional Use Only.

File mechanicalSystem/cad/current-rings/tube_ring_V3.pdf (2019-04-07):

1

B | B

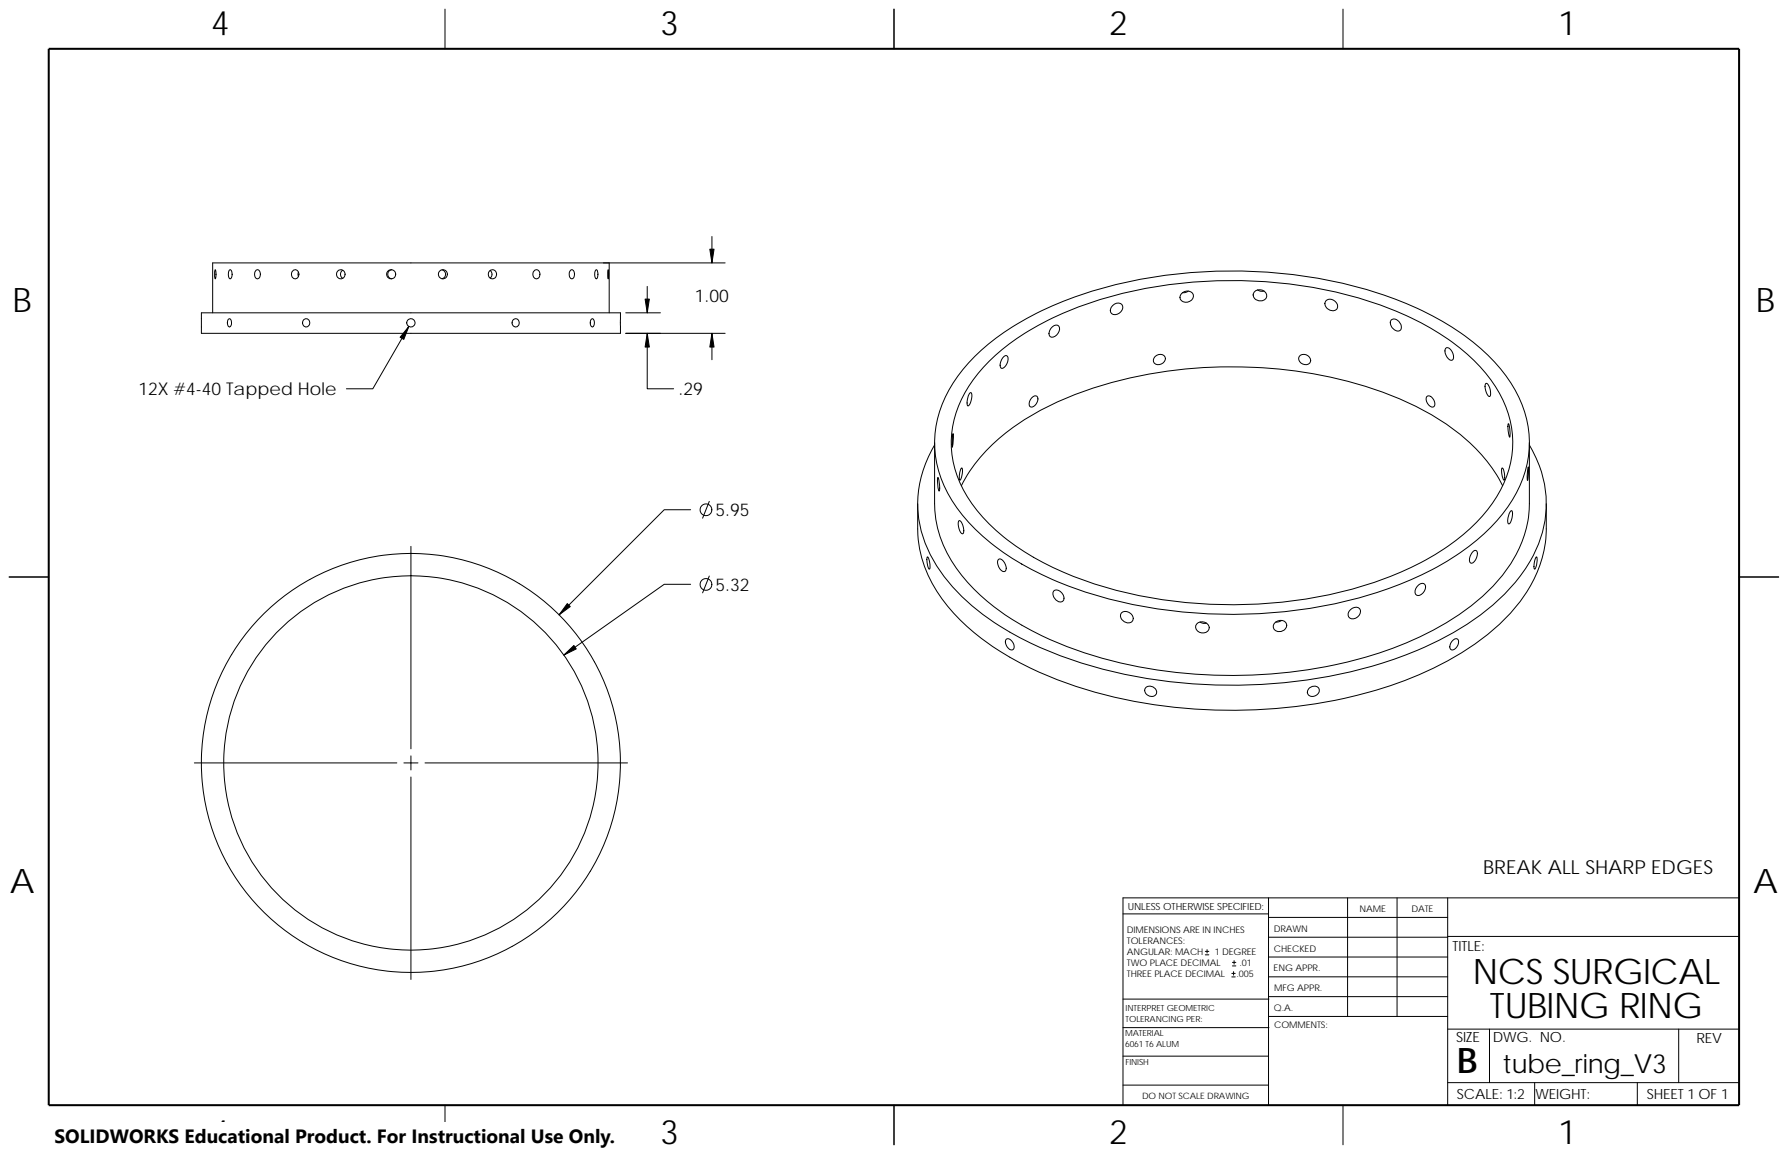
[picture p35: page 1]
6061 T6 ALUM; SCALE: 1:2; FINISH; MATERIAL; DO NOT SCALE DRAWING; SHEET 1 OF 1; DWG. NO.; WEIGHT:; REV; B tube_ring_V3; SIZE; COMMENTS:; 12X #4-40 Tapped Hole

BREAK ALL SHARP EDGES

UNLESS OTHERWISE SPECIFIED: | | NAME | DATE
CHECKED | | | TITLE: NCS SURGICAL TUBING RING

DIMENSIONS ARE IN INCHES TOLERANCES: ANGULAR: MACH 1 DEGREE TWO PLACE DECIMAL .01 THREE PLACE DECIMAL .005 INTERPRET GEOMETRIC | DRAWN

ENG APPR.
MFG APPR.

TOLERANCING PER: | Q.A.

SOLIDWORKS Educational Product. For Instructional Use Only.

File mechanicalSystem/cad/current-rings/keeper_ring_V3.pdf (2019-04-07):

B | B

4

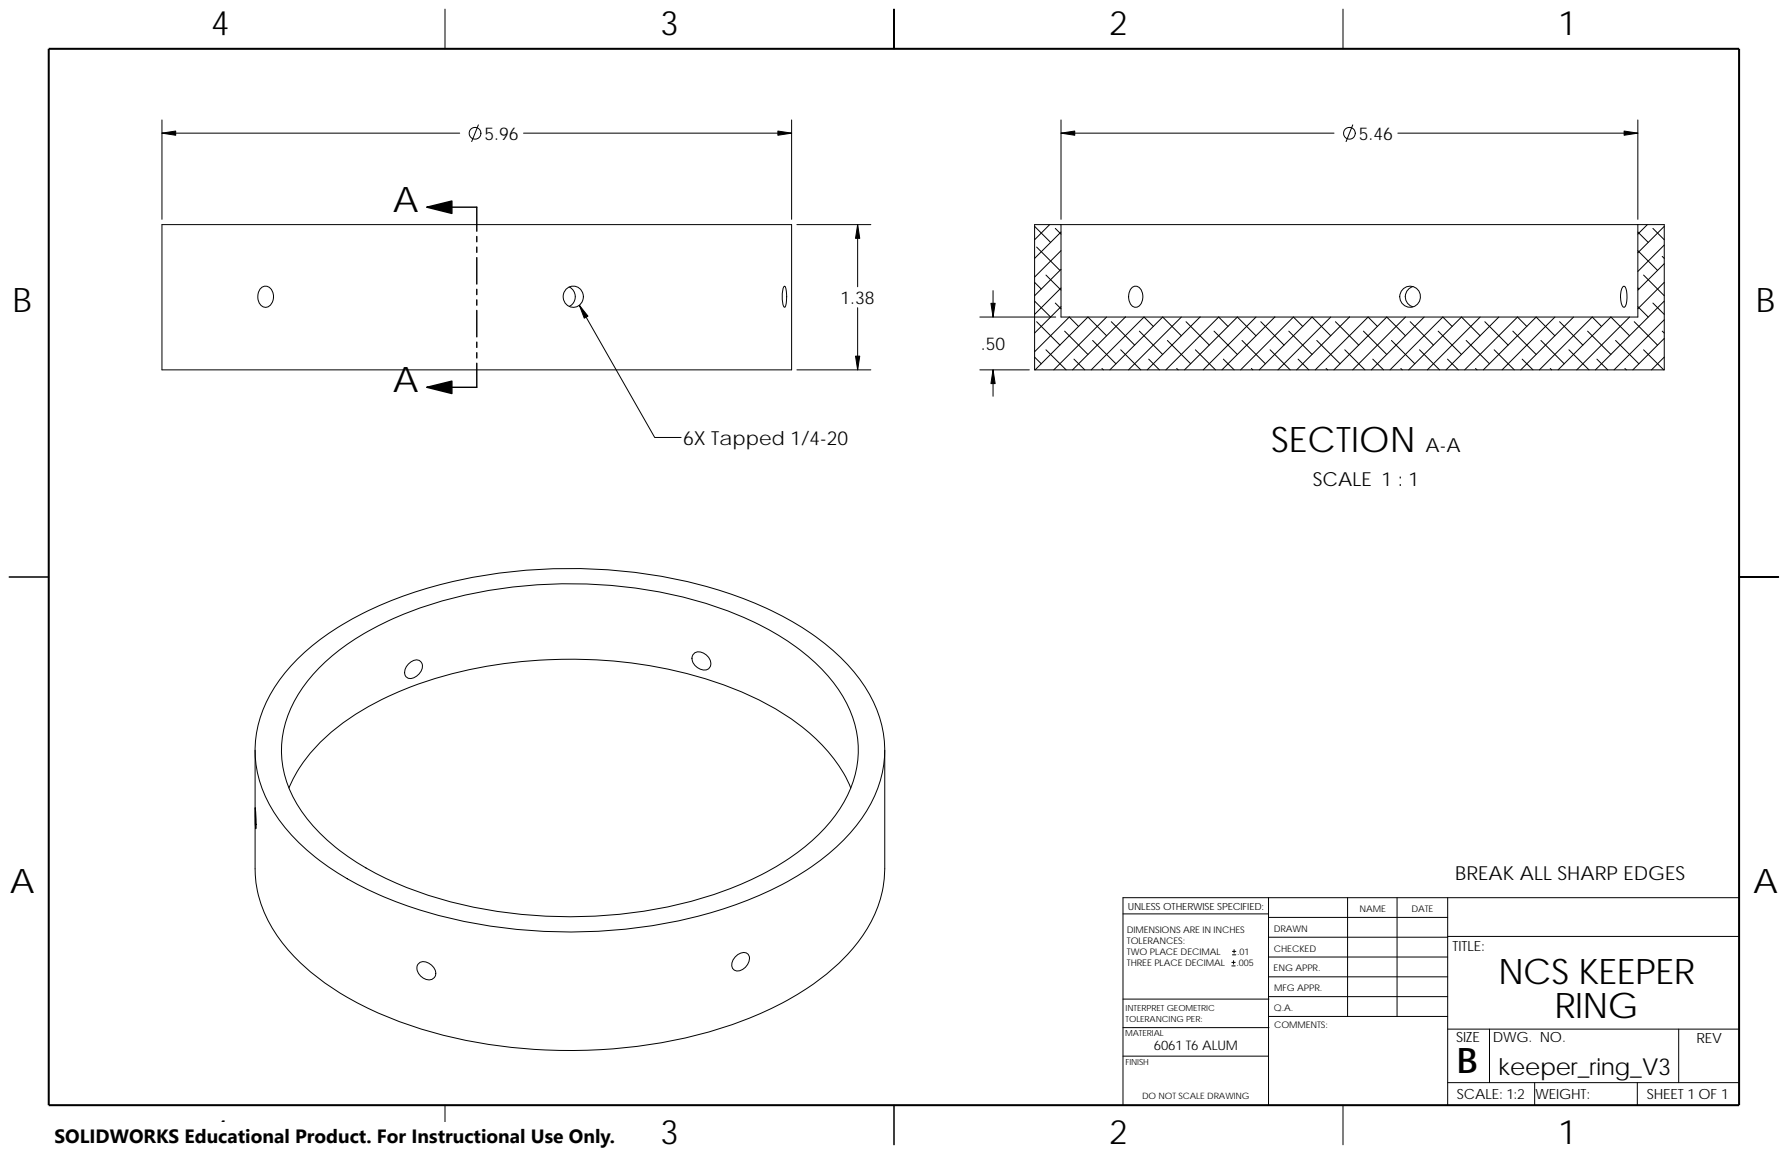
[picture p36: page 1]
DWG. NO.; MATERIAL keeper_ring_V3 FINISH; DO NOT SCALE DRAWING; SHEET 1 OF 1; WEIGHT:; REV; SCALE: 1:2; SIZE; COMMENTS:; 6061 T6 ALUM; 6X Tapped 1/4-20; SECTION A-A; SCALE 1 : 1

BREAK ALL SHARP EDGES

UNLESS OTHERWISE SPECIFIED: | | NAME | DATE

DIMENSIONS ARE IN INCHES TOLERANCES: TWO PLACE DECIMAL .01 THREE PLACE DECIMAL .005 | DRAWN

CHECKED | | | TITLE: NCS KEEPER RING

ENG APPR.
MFG APPR.

INTERPRET GEOMETRIC TOLERANCING PER: | Q.A.

SOLIDWORKS Educational Product. For Instructional Use Only.

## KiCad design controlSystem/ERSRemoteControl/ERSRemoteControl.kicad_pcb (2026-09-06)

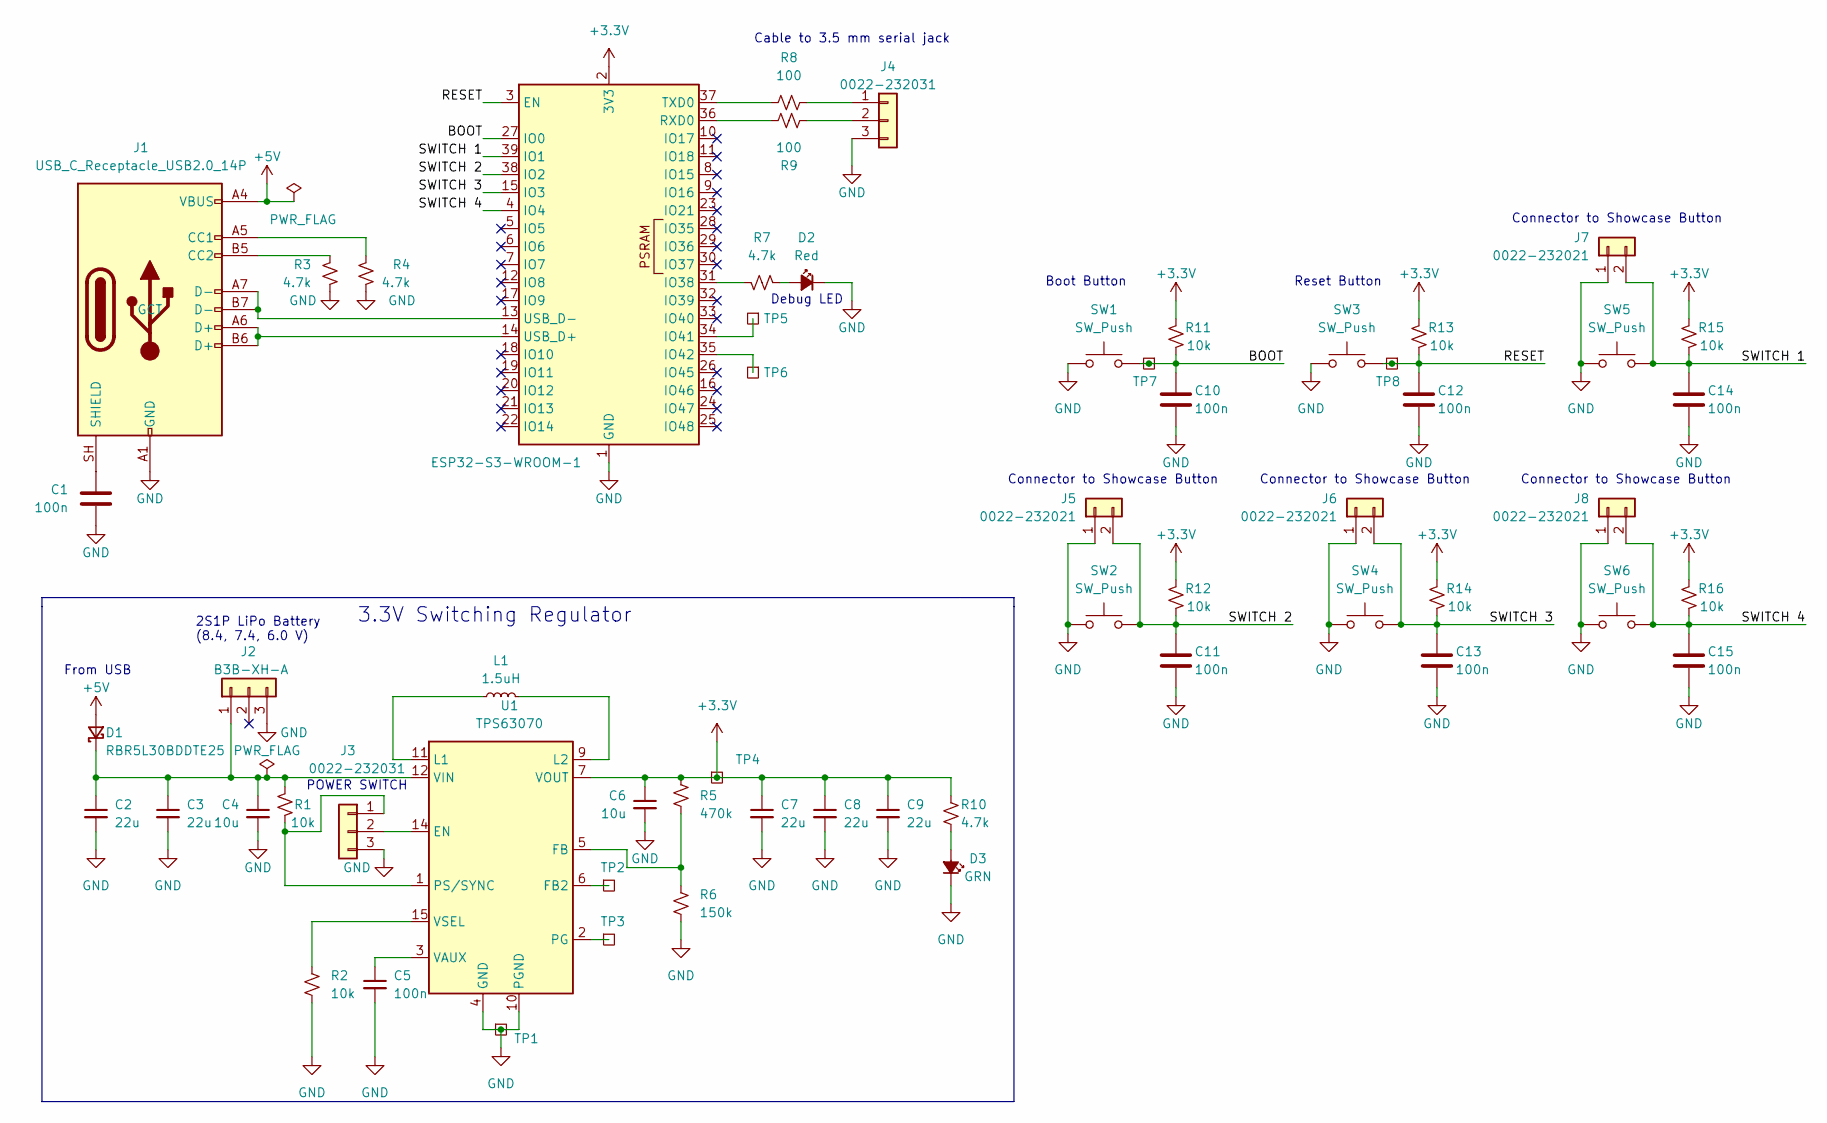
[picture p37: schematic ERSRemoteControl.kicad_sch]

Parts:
C1, C5, C10, C11, C12, C13, C14, C15: 100n; C_0603_1608Metric; MPN CL10B104KB8WPNC
C2, C3, C7, C8, C9: 22u; C_0805_2012Metric; MPN GRT21BC81C226ME13L
C4, C6: 10u; C_0805_2012Metric; MPN GRT21BC71E106KE13K
D1: RBR5L30BDDTE25; D_SMA; MPN RBR5L30BDDTE25
D2: Red; LED_0603_1608Metric; MPN 150060SS75000
D3: GRN; LED_0603_1608Metric; MPN 150060GS75000
J1: USB_C_Receptacle_USB2.0_14P; USB_C_Receptacle_Palconn_UTC16-G; MPN USB4105-GF-A
J2: B3B-XH-A; JST_XH_B3B-XH-A_1x03_P2.50mm_Vertical; MPN B3B-XH-A
J3, J4: 0022-232031; Molex_KK-254_AE-6410-03A_1x03_P2.54mm_Vertical; MPN 22232031
J5, J6, J7, J8: 0022-232021; Molex_KK-254_AE-6410-02A_1x02_P2.54mm_Vertical; MPN 22232021
L1: 1.5uH; L_Vishay_IHLP-2020; MPN IHLP2020CZER1R5M11
R1, R2, R11, R12, R13, R14, R15, R16: 10k; R_0603_1608Metric; MPN RC0603FR-0710KL
R3, R4, R7, R10: 4.7k; R_0603_1608Metric; MPN RMCF0603FT4K70
R5: 470k; R_0603_1608Metric; MPN RMCF0603FT470K
R6: 150k; R_0603_1608Metric; MPN RC0603FR-07150KL
R8, R9: 100; R_0603_1608Metric; MPN RC0603FR-07100RL
SW1, SW2, SW3, SW4, SW5, SW6: SW_Push; SW_PUSH_6mm; MPN B3F-1000
TP1, TP2, TP3, TP4, TP5, TP6, TP7, TP8: Test-Point; TP-through-hole-1X01
U1: TPS63070; U-TI-TPS63070; MPN TPS63070RNMR
U2: ESP32-S3-WROOM-1; MPN ESP32-S3-WROOM-1-N4R8

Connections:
+3.3V: C6.1, C7.1, C8.1, C9.1, R5.1, R10.1, R11.1, R12.1, R13.1, R14.1, R15.1, R16.1, TP4.1 (1_1), U1.7 (VOUT), U1.8 (VOUT), U1.TIE2 (VOUT), U2.2 (3V3)
+5V: D1.2 (A), J1.A4 (VBUS), J1.A9 (VBUS), J1.B4 (VBUS), J1.B9 (VBUS)
/BOOT: C10.1, R11.2, SW1.1, TP7.1 (1_1), U2.27 (IO0)
/RESET: C12.1, R13.2, SW3.1, TP8.1 (1_1), U2.3 (EN)
/SWITCH 1: C14.1, J7.2, R15.2, SW5.1, U2.39 (IO1)
/SWITCH 2: C11.1, J5.2, R12.2, SW2.1, U2.38 (IO2)
/SWITCH 3: C13.1, J6.2, R14.2, SW4.1, U2.15 (IO3)
/SWITCH 4: C15.1, J8.2, R16.2, SW6.1, U2.4 (IO4)
GND: C1.2, C2.2, C3.2, C4.2, C5.2, C6.2, C7.2, C8.2, C9.2, C10.2, C11.2, C12.2, C13.2, C14.2, C15.2, D2.1 (K), D3.1 (K), J1.A1 (GND), J1.A12 (GND), J1.B1 (GND), J1.B12 (GND), J2.3, J3.3, J4.3, J5.1, J6.1, J7.1, J8.1, R2.2, R3.2, R4.2, R6.2, SW1.2, SW2.2, SW3.2, SW4.2, SW5.2, SW6.2, TP1.1 (1_1), U1.4 (GND), U1.10 (PGND), U2.1 (GND), U2.40 (GND), U2.41 (GND)
unnamed: C2.1, C3.1, C4.1, D1.1 (K), J2.1, R1.2, U1.12 (VIN), U1.13 (VIN), U1.TIE1 (VIN)
unnamed: D2.2 (A), R7.1
unnamed: D3.2 (A), R10.2
unnamed: J1.A5 (CC1), R4.1
unnamed: J1.B5 (CC2), R3.1
unnamed: C1.1, J1.SH (SHIELD)
unnamed: J3.1, R1.1, U1.1 (PS/SYNC)
unnamed: J3.2, U1.14 (EN)
unnamed: J4.1, R8.2
unnamed: J4.2, R9.1
unnamed: TP2.1 (1_1), U1.6 (FB2)
unnamed: R5.2, R6.1, U1.5 (FB)
unnamed: L1.1, U1.11 (L1)
unnamed: L1.2, U1.9 (L2)
unnamed: TP3.1 (1_1), U1.2 (PG)
unnamed: C5.1, U1.3 (VAUX)
unnamed: R2.1, U1.15 (VSEL)
unnamed: R7.2, U2.31 (IO38)
unnamed: TP5.1 (1_1), U2.34 (IO41)
unnamed: TP6.1 (1_1), U2.35 (IO42)
unnamed: R9.2, U2.36 (RXD0)
unnamed: R8.1, U2.37 (TXD0)
unnamed: J1.A6 (D+), J1.B6 (D+), U2.14 (USB_D+)
unnamed: J1.A7 (D-), J1.B7 (D-), U2.13 (USB_D-)

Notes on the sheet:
Reset Button
3.3V Switching Regulator
2S1P LiPo Battery (8.4, 7.4, 6.0 V)
Connector to Showcase Button
Boot Button
Cable to 3.5 mm serial jack
From USB
POWER SWITCH
Debug LED

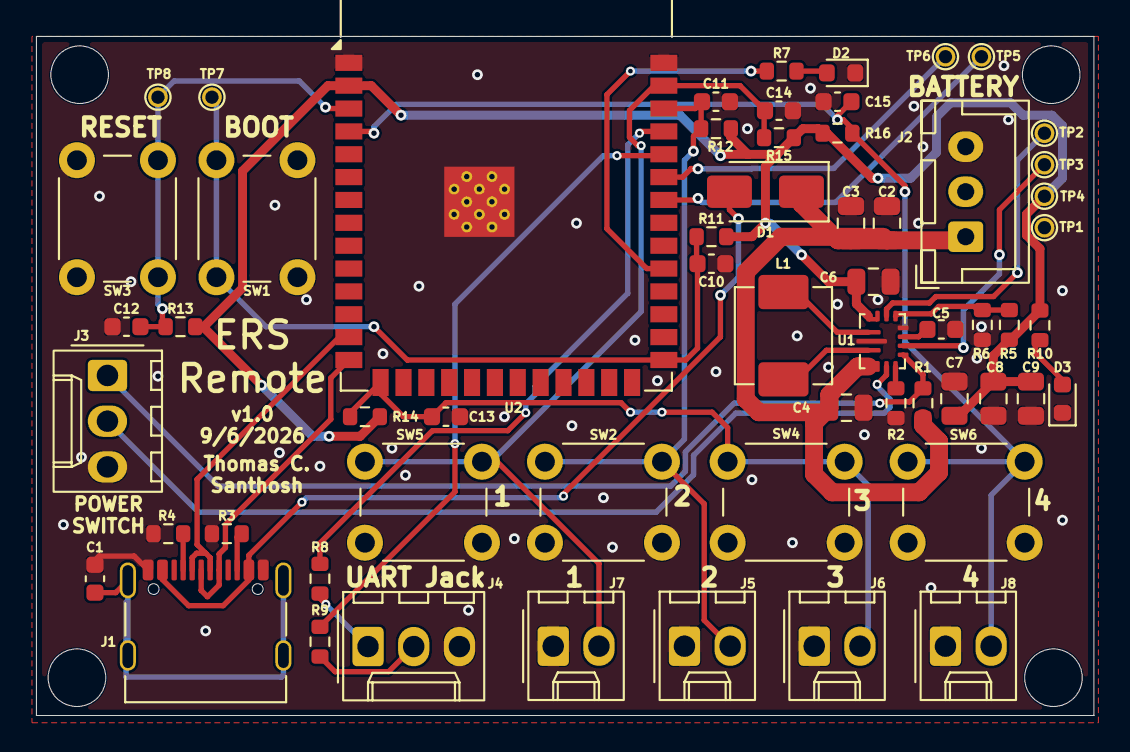
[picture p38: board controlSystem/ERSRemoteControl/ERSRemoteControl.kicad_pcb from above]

Board: 2 copper layers, 58.8 x 37.7 mm, 59 parts (0 on the bottom side), 33 nets.

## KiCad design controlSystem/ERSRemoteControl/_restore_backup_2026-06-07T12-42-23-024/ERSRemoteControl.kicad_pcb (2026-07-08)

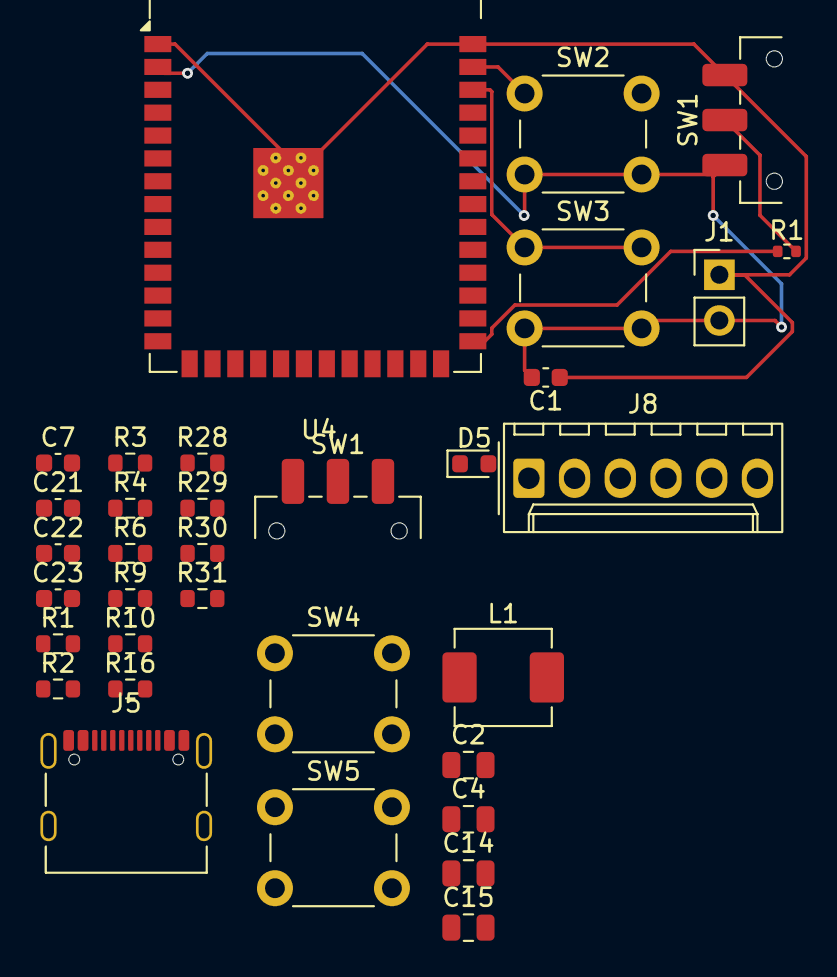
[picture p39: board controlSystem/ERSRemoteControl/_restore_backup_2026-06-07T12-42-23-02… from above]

Board: 2 copper layers, 34 parts (0 on the bottom side), 17 nets.

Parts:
C1, C7, C21, C22, C23: 100n; C_0603_1608Metric
C2, C4, C14, C15: 22u; C_0805_2012Metric
D5: GRN; LED_0603_1608Metric
J1: Conn_01x02_Socket; PinHeader_1x02_P2.54mm_Vertical
J5: USB_C_Receptacle_USB2.0_14P; USB_C_Receptacle_Palconn_UTC16-G
J8: 00222-32051; Molex_KK-254_AE-6410-06A_1x06_P2.54mm_Vertical
L1: 1.5uH; L_Vishay_IHLP-2020
R1: R_US; R_0402_1005Metric
R1#2, R2, R3: 220; R_0603_1608Metric
R4, R6, R30, R31: 10k; R_0603_1608Metric
R9: 470k; R_0603_1608Metric
R10: 150k; R_0603_1608Metric
R16, R28, R29: 4.7k; R_0603_1608Metric
SW1, SW1#2: SW_SPDT; SW_SPDT_CK_JS102011SAQN
SW2, SW3, SW4, SW5: SW_Push; SW_PUSH_6mm
U4: ESP32-S3-WROOM-1

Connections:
+3.3V: C1.1, C14.1, C15.1, J1.2, R9.1, R16.1, R30.1, R31.1, SW1.1 (A), SW1#2.1 (A), SW2.2, SW3.2, U4.2 (3V3)
+5V: C2.1, C4.1, J5.A4 (VBUS), J5.A9 (VBUS), J5.B4 (VBUS), J5.B9 (VBUS), R6.1
GND: C1.2, C2.2, C4.2, C7.2, C14.2, C15.2, C21.2, C22.2, C23.2, D5.1 (K), J1.1, J5.A1 (GND), J5.A12 (GND), J5.B1 (GND), J5.B12 (GND), R4.2, R10.2, R28.2, R29.2, SW1.3 (C), SW1#2.3 (C), SW4.2, SW5.2, U4.1 (GND), U4.40 (GND), U4.41 (GND)
unnamed: D5.2 (A), R16.2
unnamed: J5.A5 (CC1), R29.1
unnamed: J5.B5 (CC2), R28.1
unnamed: R2.2, SW2.1
unnamed: R3.2, SW3.1
unnamed: R1.2, R1#2.2, SW1.2 (B), SW1#2.2 (B)
unnamed: R9.2, R10.1
unnamed: C22.1, R30.2, SW4.1, U4.3 (EN)
unnamed: C23.1, R1.1, R31.2, SW5.1, U4.27 (IO0)
unnamed: R2.1, U4.39 (IO1)
unnamed: R3.1, U4.38 (IO2)
unnamed: R1#2.1, U4.15 (IO3)
unnamed: J5.A6 (D+), J5.B6 (D+), U4.14 (USB_D+)
unnamed: J5.A7 (D-), J5.B7 (D-), U4.13 (USB_D-)

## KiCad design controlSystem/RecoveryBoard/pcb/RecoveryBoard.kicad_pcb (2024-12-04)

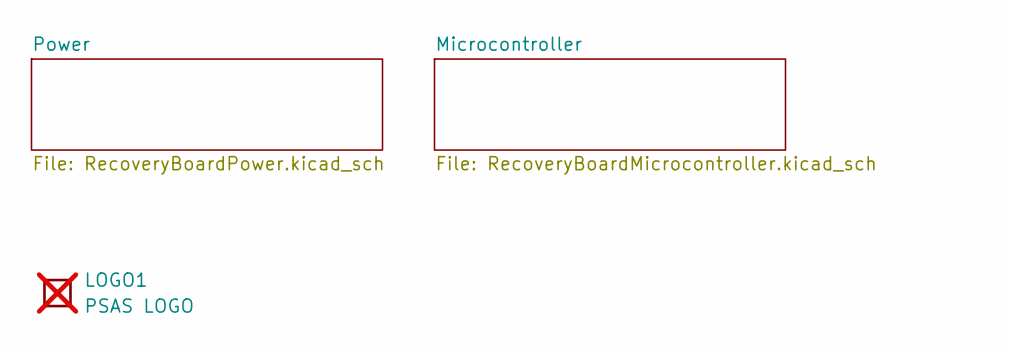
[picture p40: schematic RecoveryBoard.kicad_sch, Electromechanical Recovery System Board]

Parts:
LOGO1: PSAS LOGO; PSAS_LOGO_10X10; not fitted

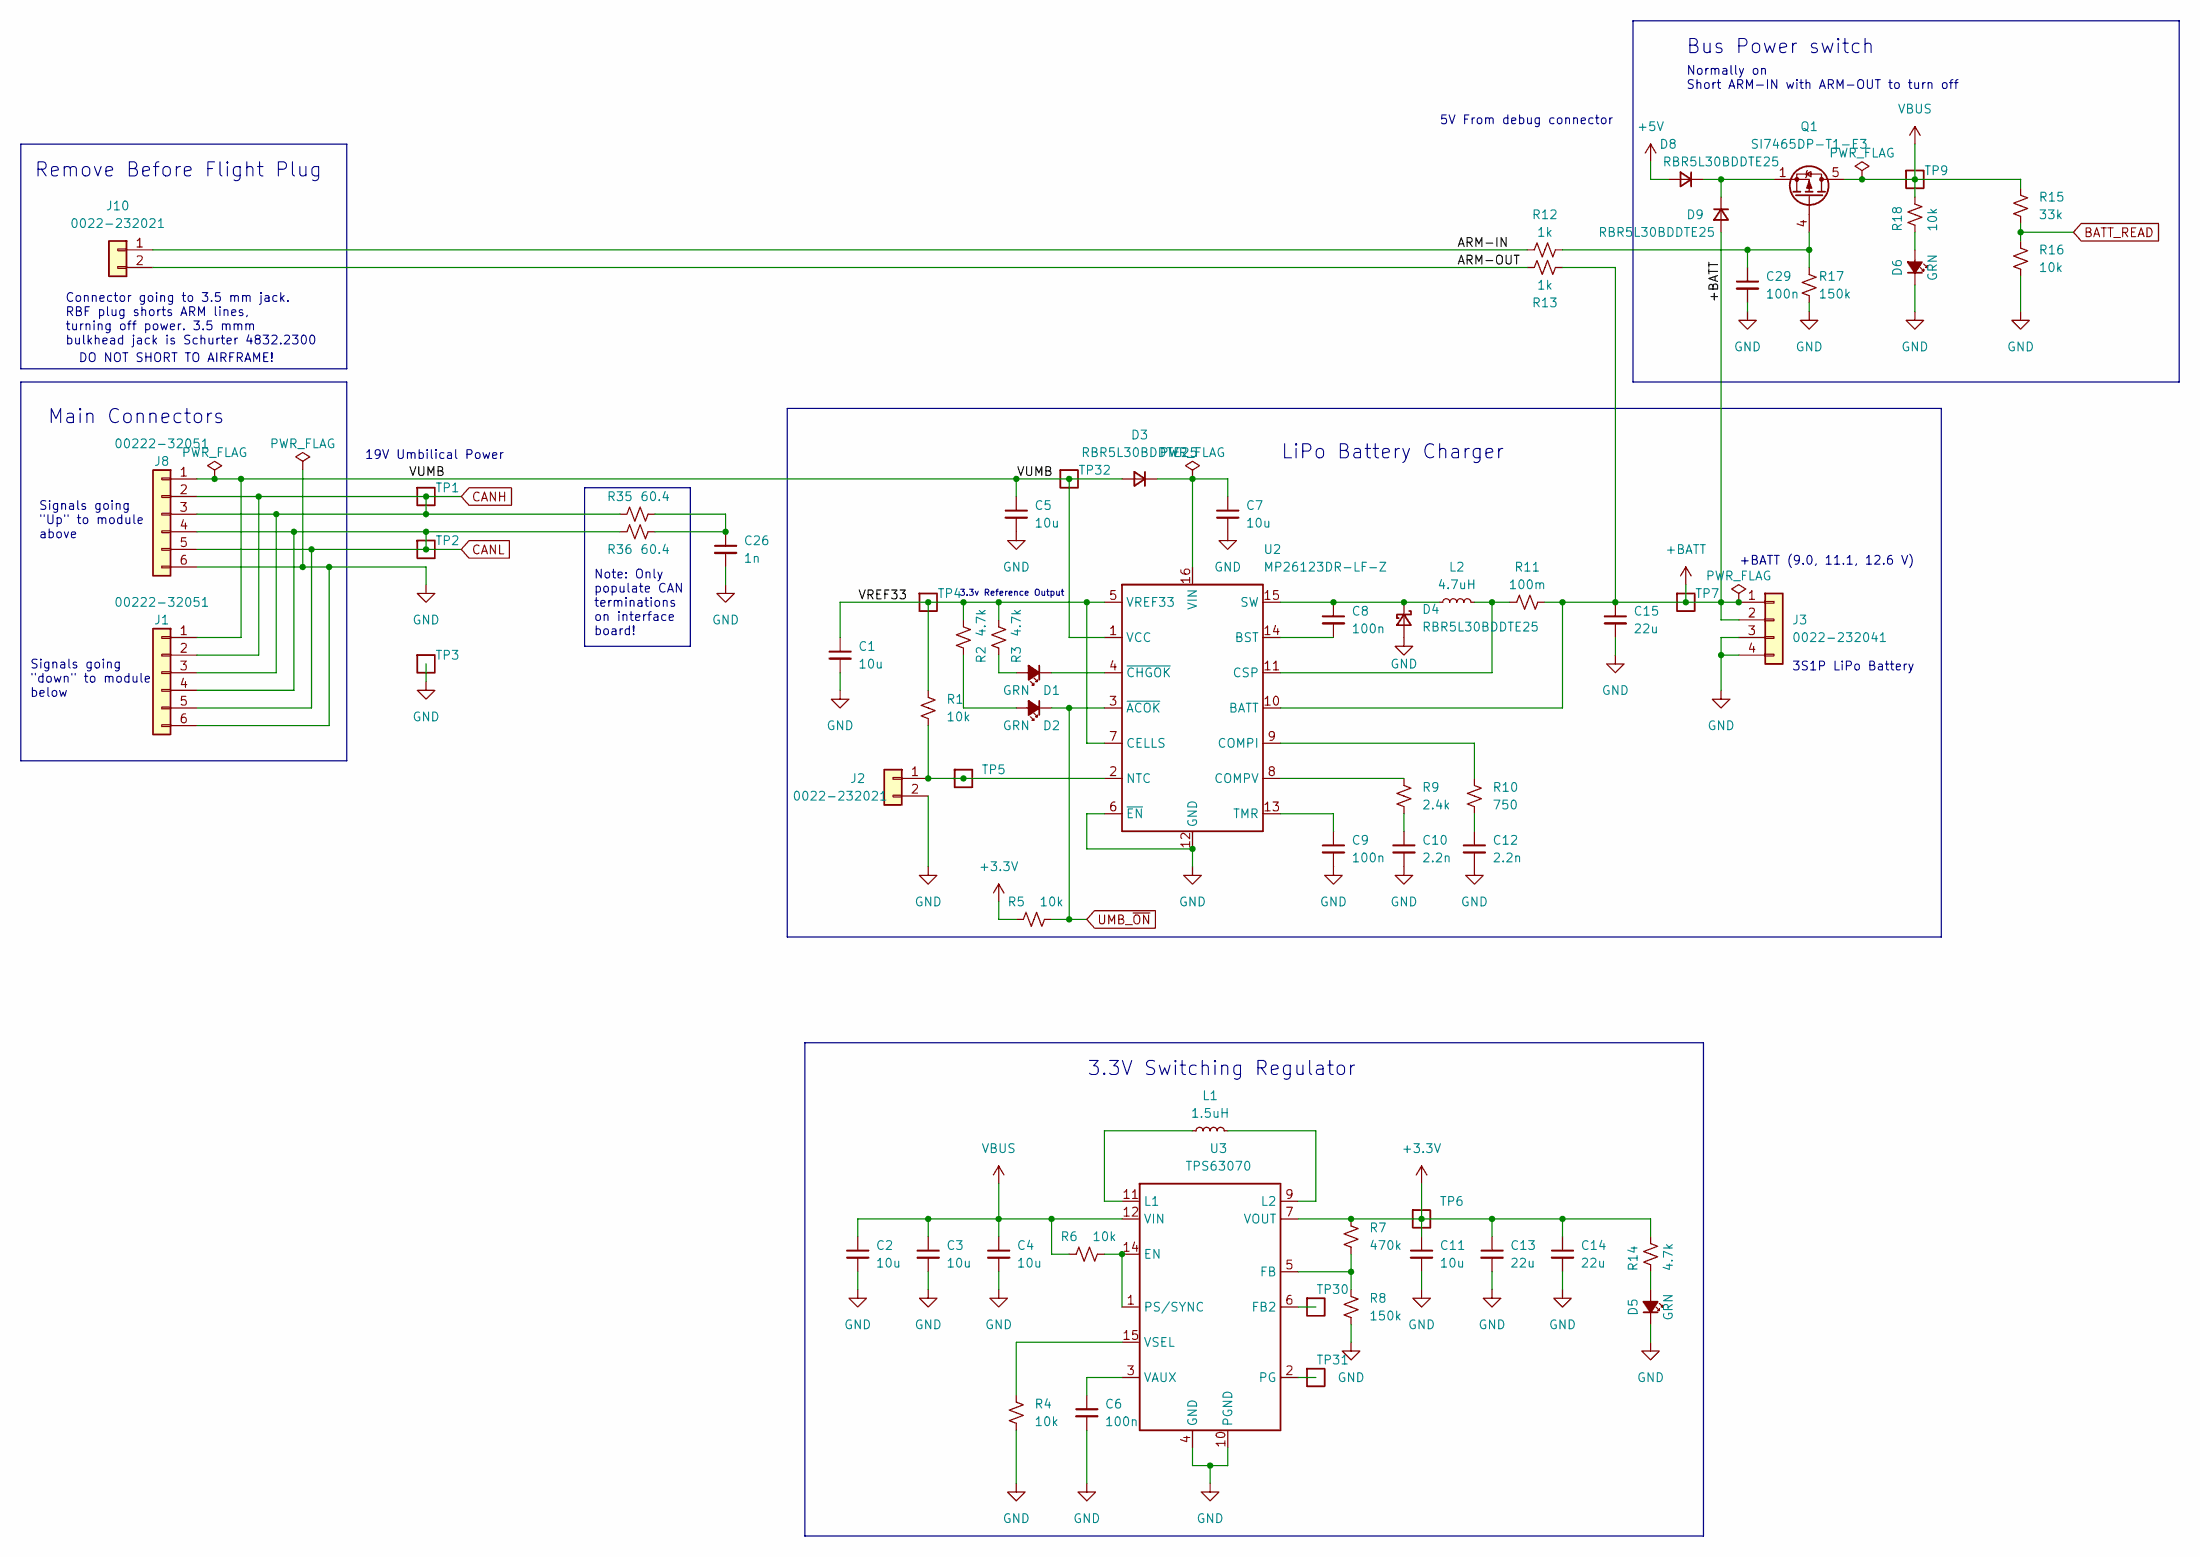
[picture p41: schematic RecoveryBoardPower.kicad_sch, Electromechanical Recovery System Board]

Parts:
C1, C2, C3, C5, C7: 10u; C_0805_2012Metric; MPN GRM21BR61H106KE43L
C4, C11: 10u; C_0603_1608Metric; MPN GRT188R61E106ME13D
C6, C8, C9, C29: 100n; C_0603_1608Metric; MPN CL10B104KB8WPNC
C10, C12: 2.2n; C_0603_1608Metric; MPN CL10B222KB8WPNC
C13, C14, C15: 22u; C_0805_2012Metric; MPN GRT21BR61E226ME13L
C26: 1n; C_0603_1608Metric; MPN CL10B102KB85PNL
D1, D2, D5, D6: GRN; LED_0603_1608Metric; MPN 150060GS75000
D3, D4, D8, D9: RBR5L30BDDTE25; D_SMA; MPN RBR5L30BDDTE25
J1, J8: 00222-32051; Molex_KK-254_AE-6410-06A_1x06_P2.54mm_Vertical; MPN 22232061
J2, J10: 0022-232021; Molex_KK-254_AE-6410-02A_1x02_P2.54mm_Vertical; MPN 22232021
J3: 0022-232041; Molex_KK-254_AE-6410-04A_1x04_P2.54mm_Vertical; MPN 22232041
L1: 1.5uH; L_Vishay_IHLP-2020; MPN IHLP2020CZER1R5M11
L2: 4.7uH; L_Vishay_IHLP-2020; MPN IHLP2020BZER4R7M11
Q1: SI7465DP-T1-E3; PowerPAK_SO-8_Single; MPN SI7141DP-T1-GE3
R1, R4, R5, R6, R16, R18: 10k; R_0603_1608Metric; MPN RC0603FR-0710KL
R2, R3, R14: 4.7k; R_0603_1608Metric; MPN RC0603FR-074K7L
R7: 470k; R_0603_1608Metric; MPN RC0603FR-07470KL
R8, R17: 150k; R_0603_1608Metric; MPN RC0603FR-07150KL
R9: 2.4k; R_0603_1608Metric; MPN RC0603FR-072K4L
R10: 750; R_0603_1608Metric; MPN RC0603FR-07750RL
R11: 100m; R_1206_3216Metric; MPN CSR1206FTR100
R12, R13: 1k; R_0603_1608Metric; MPN RC0603FR-071KL
R15: 33k; R_0603_1608Metric; MPN RC0603FR-0733KL
R35, R36: 60.4; R_1206_3216Metric; MPN RC0603FR-0760R4L
TP1, TP2, TP3, TP4, TP5, TP6, TP7, TP9, TP30, TP31, TP32: Test-Point; TP-through-hole-1X01
U2: MP26123DR-LF-Z; QFN-16-1EP_4x4mm_P0.65mm_EP2.5x2.5mm; MPN MP26123DR-LF-Z
U3: TPS63070; U-TI-TPS63070; MPN TPS63070RNMR

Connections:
+3.3V: C11.1, C13.1, C14.1, R5.1, R7.1, R14.1, TP6.1, U3.7 (VOUT), U3.8 (VOUT), U3.TIE2 (VOUT); also elsewhere on the board
+5V: D8.2 (A); also elsewhere on the board
+BATT: C15.1, D9.2 (A), J3.1, J3.2, R11.2, R13.1, TP7.1, U2.10 (BATT)
/Power/ARM-IN: J10.1, R12.1
/Power/ARM-OUT: J10.2, R13.2
/Power/VREF33: C1.1, R1.1, R2.1, R3.1, TP4.1, U2.5 (VREF33), U2.7 (CELLS)
/Power/VUMB: C5.1, D3.2 (A), J1.1, J8.1, TP32.1, U2.1 (VCC)
BATT_READ: R15.2, R16.1; also elsewhere on the board
CANH: J1.2, J1.3, J8.2, J8.3, R35.1, TP1.1; also elsewhere on the board
CANL: J1.4, J1.5, J8.4, J8.5, R36.2, TP2.1; also elsewhere on the board
GND: C1.2, C2.2, C3.2, C4.2, C5.2, C6.2, C7.2, C9.2, C10.2, C11.2, C12.2, C13.2, C14.2, C15.2, C26.2, C29.2, D4.2 (A), D5.1 (K), D6.1 (K), J1.6, J2.2, J3.3, J3.4, J8.6, R4.2, R8.2, R16.2, R17.2, TP3.1, U2.6 (~EN), U2.12 (GND), U2.17 (GND), U3.4 (GND), U3.10 (PGND); also elsewhere on the board
unnamed: C10.1, R9.2
unnamed: C12.1, R10.2
unnamed: C26.1, R35.2, R36.1
unnamed: D1.2 (A), R3.2
unnamed: D1.1 (K), U2.4 (~CHGOK)
unnamed: D2.2 (A), R2.2
unnamed: C7.1, D3.1 (K), U2.16 (VIN)
unnamed: C8.1, D4.1 (K), L2.1, U2.15 (SW)
unnamed: D5.2 (A), R14.2
unnamed: D6.2 (A), R18.2
unnamed: D8.1 (K), D9.1 (K), Q1.1 (S), Q1.2 (S), Q1.3 (S)
unnamed: J2.1, R1.2, TP5.1, U2.2 (NTC)
unnamed: C29.1, Q1.4 (G), R12.2, R17.1
unnamed: C8.2, U2.14 (BST)
unnamed: R10.1, U2.9 (COMPI)
unnamed: R9.1, U2.8 (COMPV)
unnamed: L2.2, R11.1, U2.11 (CSP)
unnamed: C9.1, U2.13 (TMR)
unnamed: R6.2, U3.1 (PS/SYNC), U3.14 (EN)
unnamed: TP30.1, U3.6 (FB2)
unnamed: R7.2, R8.1, U3.5 (FB)
unnamed: L1.1, U3.11 (L1)
unnamed: L1.2, U3.9 (L2)
unnamed: TP31.1, U3.2 (PG)
unnamed: C6.1, U3.3 (VAUX)
unnamed: R4.1, U3.15 (VSEL)
UMB_~ON: D2.1 (K), R5.2, U2.3 (~ACOK); also elsewhere on the board
VBUS: C2.1, C3.1, C4.1, Q1.5 (D), R6.1, R15.1, R18.1, TP9.1, U3.12 (VIN), U3.13 (VIN), U3.TIE1 (VIN); also elsewhere on the board

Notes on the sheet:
3.3v Reference Output
Remove Before Flight Plug
3.3V Switching Regulator
Note: Only populate CAN terminations on interface board!
19V Umbilical Power
Bus Power switch
DO NOT SHORT TO AIRFRAME!
3S1P LiPo Battery
5V From debug connector
+BATT (9.0, 11.1, 12.6 V)
Signals going "Up" to module above
Normally on Short ARM-IN with ARM-OUT to turn off
Main Connectors
Connector going to 3.5 mm jack. RBF plug shorts ARM lines, turning off power. 3.5 mmm bulkhead jack is Schurter 4832.2300
Signals going "down" to module below
LiPo Battery Charger

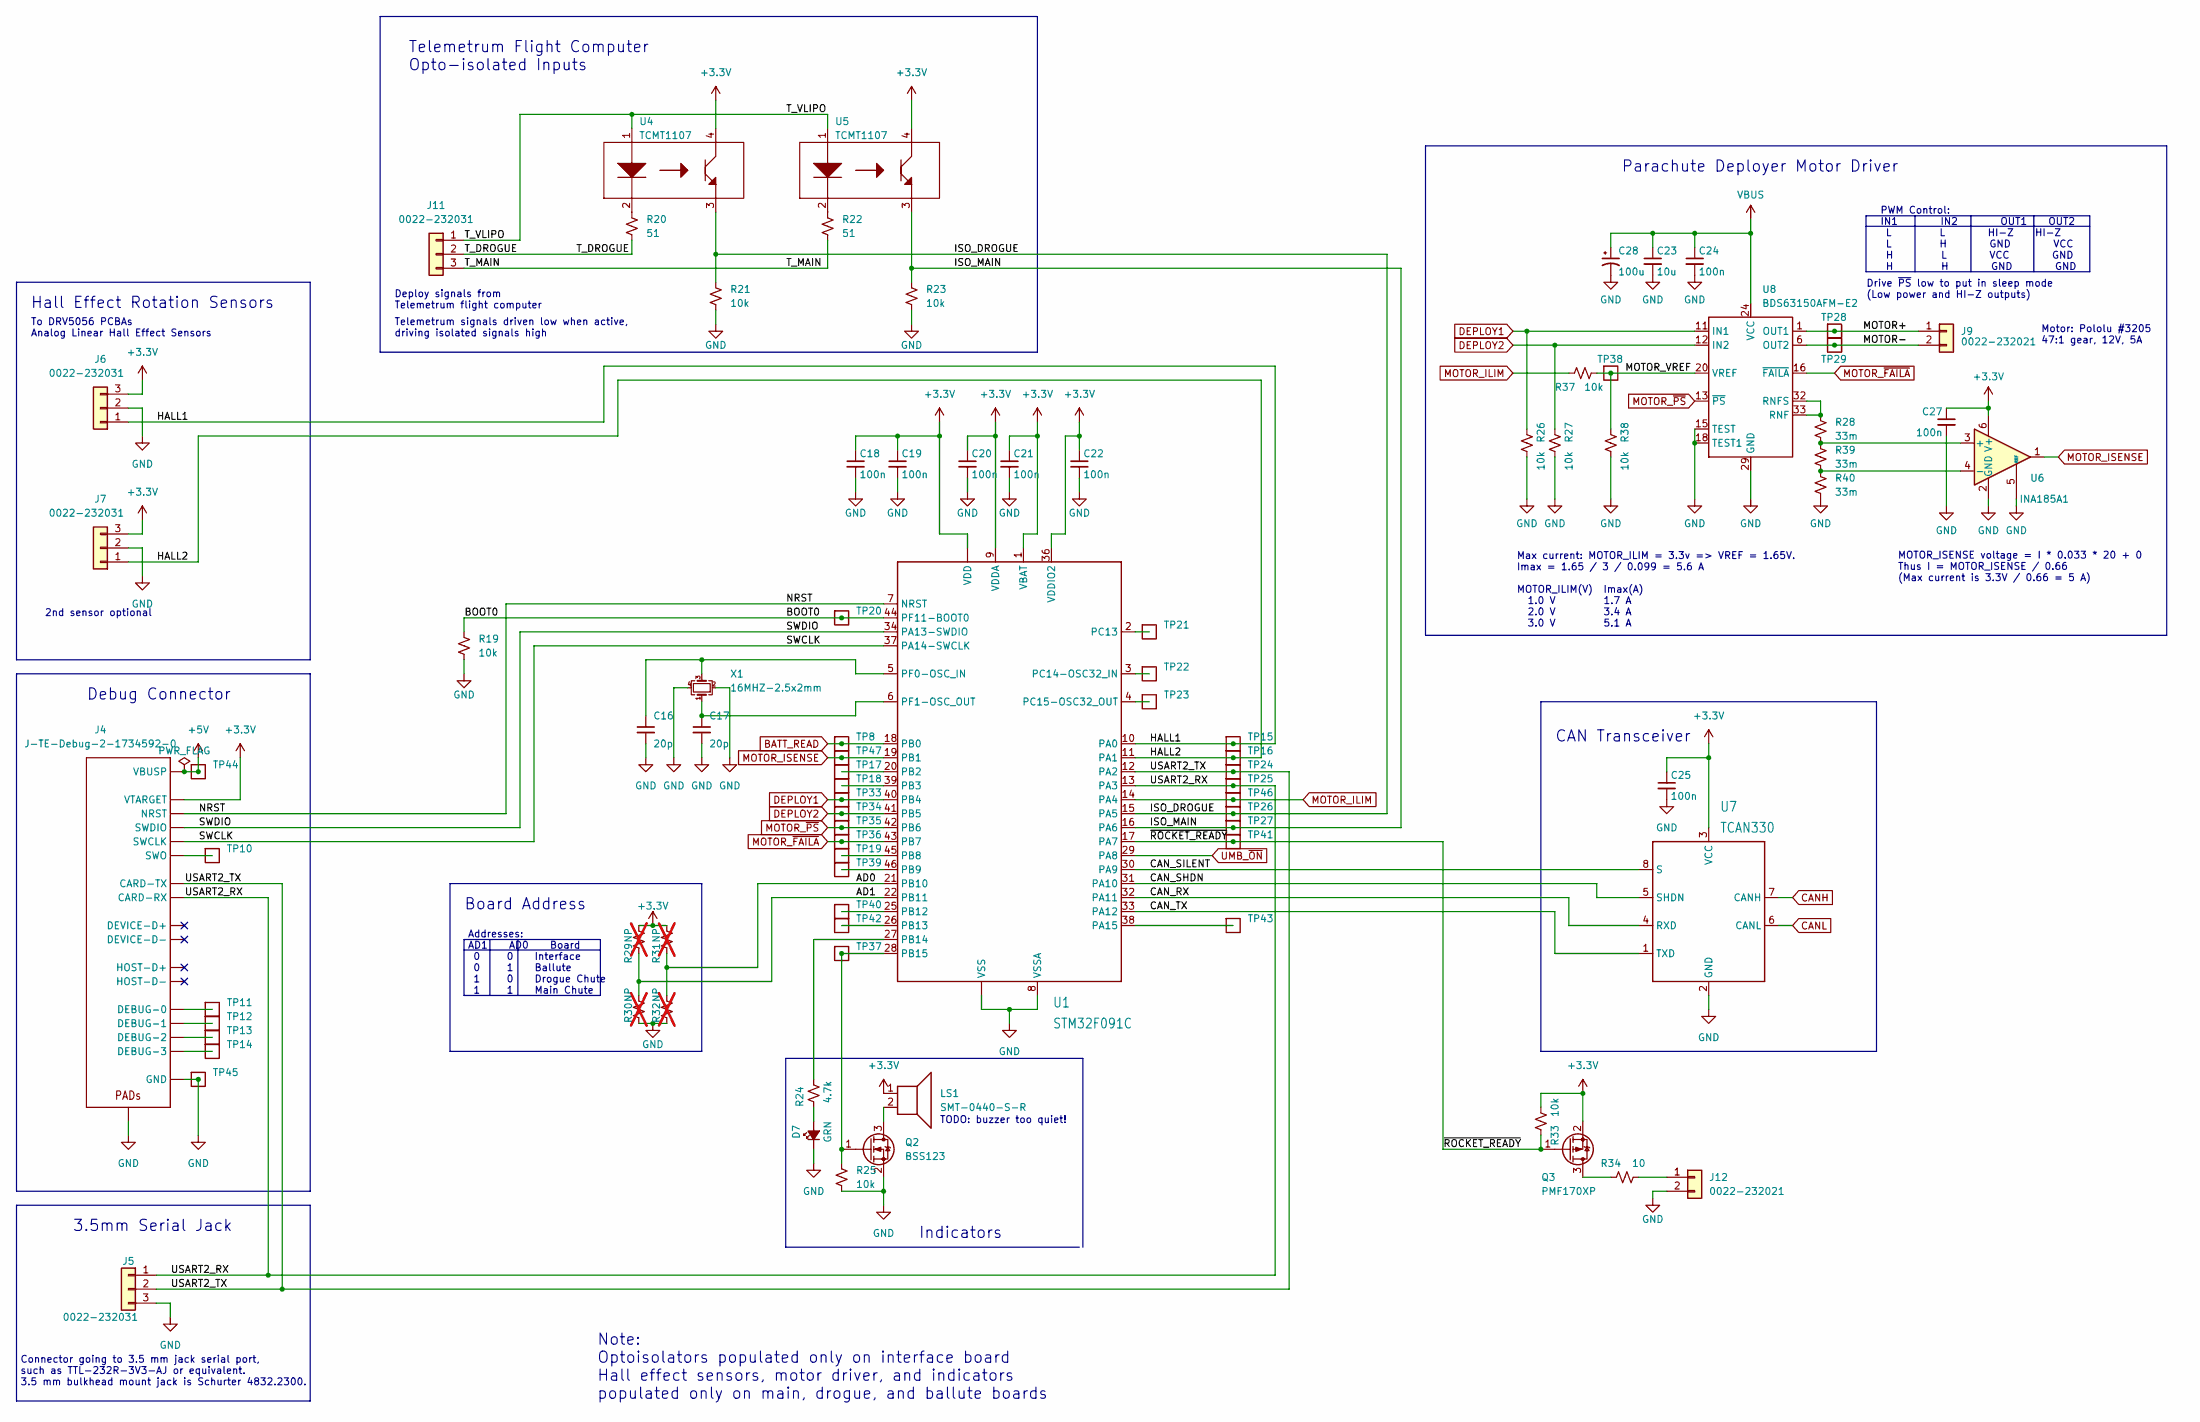
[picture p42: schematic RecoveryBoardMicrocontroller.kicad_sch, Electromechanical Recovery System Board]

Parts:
C16, C17: 20p; C_0603_1608Metric; MPN C0603C200G4HAC7867
C18, C19, C20, C21, C22, C24, C25, C27: 100n; C_0603_1608Metric; MPN CL10B104KB8WPNC
C23: 10u; C_0805_2012Metric; MPN GRM21BR61H106KE43L
C28: 100u; CP_EIA-7343-43_Kemet-X; MPN T491X107K020AT
D7: GRN; LED_0603_1608Metric; MPN 150060GS75000
J4: J-TE-Debug-2-1734592-0; J-TE_2-1734592-0; MPN 2-1734592-0
J5, J6, J7, J11: 0022-232031; Molex_KK-254_AE-6410-03A_1x03_P2.54mm_Vertical; MPN 22232031
J9, J12: 0022-232021; Molex_KK-254_AE-6410-02A_1x02_P2.54mm_Vertical; MPN 22232021
LS1: SMT-0440-S-R; MPN SMT-0440-S-R
Q2: BSS123; SOT-23; MPN BSS123
Q3: PMF170XP; SOT-323_SC-70; MPN PMF170XP,115
R19, R21, R23, R25, R26, R27, R33, R37, R38: 10k; R_0603_1608Metric; MPN RC0603FR-0710KL
R20, R22: 51; R_0603_1608Metric; MPN RC0603FR-0751RL
R24: 4.7k; R_0603_1608Metric; MPN RC0603FR-074K7L
R28, R39, R40: 33m; R_1206_3216Metric; MPN RLP73M2BR033FTDF
R29, R30, R31, R32: NP; R_0603_1608Metric; not fitted
R34: 10; R_0603_1608Metric; MPN RC0603FR-0710RL
TP8, TP10, TP11, TP12, TP13, TP14, TP15, TP16, TP17, TP18, TP19, TP20, TP21, TP22, TP23, TP24, TP25, TP26, TP27, TP28, TP29, TP33, TP34, TP35, TP36, TP37, TP38, TP39, TP40, TP41, TP42, TP43, TP44, TP45, TP46, TP47: Test-Point; TP-through-hole-1X01
U1: STM32F091C; LQFP-48_7x7mm_P0.5mm; MPN STM32F091CCT7
U4, U5: TCMT1107; SOP-4_4.4x2.6mm_P1.27mm; MPN TCMT1107
U6: INA185A1; SOT-563; MPN INA185A1IDRLR
U7: TCAN330; SOT23-8; MPN TCAN330GDCNT
U8: BDS63150AFM-E2; U-BD63150AFM; MPN BD63150AFM-E2
X1: 16MHZ-2.5x2mm; Crystal_SMD_2520-4Pin_2.5x2.0mm; MPN ECS-160-10-36Q-ES-TR

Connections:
+3.3V: C18.1, C19.1, C20.1, C21.1, C22.1, C25.1, C27.1, J4.11 (VTARGET), J6.3, J7.3, LS1.1, Q3.2 (S), R29.1, R31.1, R33.2, U1.1 (VBAT), U1.9 (VDDA), U1.24 (VDD), U1.36 (VDDIO2), U1.48 (VDD), U4.4 (IN), U5.4 (IN), U6.6 (V+), U7.3 (VCC); also elsewhere on the board
+5V: J4.1 (VBUSP), J4.2 (VBUSP), TP44.1; also elsewhere on the board
/Microcontroller/AD0: R31.2, R32.1, U1.21 (PB10)
/Microcontroller/AD1: R29.2, R30.1, U1.22 (PB11)
/Microcontroller/BOOT0: R19.1, TP20.1, U1.44 (PF11-BOOT0)
/Microcontroller/CAN_RX: U1.32 (PA11), U7.4 (RXD)
/Microcontroller/CAN_SHDN: U1.31 (PA10), U7.5 (SHDN)
/Microcontroller/CAN_SILENT: U1.30 (PA9), U7.8 (S)
/Microcontroller/CAN_TX: U1.33 (PA12), U7.1 (TXD)
/Microcontroller/HALL1: J6.1, TP15.1, U1.10 (PA0)
/Microcontroller/HALL2: J7.1, TP16.1, U1.11 (PA1)
/Microcontroller/ISO_DROGUE: R21.1, TP26.1, U1.15 (PA5), U4.3 (OUT)
/Microcontroller/ISO_MAIN: R23.1, TP27.1, U1.16 (PA6), U5.3 (OUT)
/Microcontroller/MOTOR+: J9.1, TP28.1, U8.1 (OUT1), U8.2 (OUT1), U8.3 (OUT1)
/Microcontroller/MOTOR-: J9.2, TP29.1, U8.6 (OUT2), U8.7 (OUT2), U8.8 (OUT2)
/Microcontroller/MOTOR_VREF: R37.2, R38.1, TP38.1, U8.20 (VREF)
/Microcontroller/NRST: J4.10 (NRST), U1.7 (NRST)
/Microcontroller/SWCLK: J4.15 (SWCLK), U1.37 (PA14-SWCLK)
/Microcontroller/SWDIO: J4.14 (SWDIO), U1.34 (PA13-SWDIO)
/Microcontroller/T_DROGUE: J11.2, R20.2
/Microcontroller/T_MAIN: J11.3, R22.2
/Microcontroller/T_VLIPO: J11.1, U4.1 (A), U5.1 (A)
/Microcontroller/USART2_RX: J4.12 (CARD-RX), J5.1, TP25.1, U1.13 (PA3)
/Microcontroller/USART2_TX: J4.13 (CARD-TX), J5.2, TP24.1, U1.12 (PA2)
/Microcontroller/~ROCKET_READY: Q3.1 (G), R33.1, TP41.1, U1.17 (PA7)
BATT_READ: TP8.1, U1.18 (PB0); also elsewhere on the board
CANH: U7.7 (CANH); also elsewhere on the board
CANL: U7.6 (CANL); also elsewhere on the board
DEPLOY1: R26.1, TP33.1, U1.40 (PB4), U8.11 (IN1)
DEPLOY2: R27.1, TP34.1, U1.41 (PB5), U8.12 (IN2)
GND: C16.2, C17.2, C18.2, C19.2, C20.2, C21.2, C22.2, C23.2, C24.2, C25.2, C27.2, C28.2, D7.1 (K), J4.3 (GND), J4.6 (GND), J4.9 (GND), J4.PAD1 (PAD), J4.PAD2 (PAD), J5.3, J6.2, J7.2, J12.2, Q2.2 (S), R19.2, R21.2, R23.2, R25.2, R26.2, R27.2, R30.2, R32.2, R38.2, R40.2, TP45.1, U1.8 (VSSA), U1.23 (VSS), U1.35 (VSS), U1.47 (VSS), U6.2 (GND), U6.5 (REF), U7.2 (GND), U8.15 (TEST), U8.18 (TEST1), U8.22 (GND), U8.29 (GND), U8.37 (GND), U8.38 (GND), X1.2, X1.4; also elsewhere on the board
MOTOR_ILIM: R37.1, TP46.1, U1.14 (PA4)
MOTOR_ISENSE: TP47.1, U1.19 (PB1), U6.1
MOTOR_~FAILA: TP36.1, U1.43 (PB7), U8.16 (~FAILA)
MOTOR_~PS: TP35.1, U1.42 (PB6), U8.13 (~PS)
unnamed: D7.2 (A), R24.2
unnamed: J4.17 (DEBUG-0), TP11.1
unnamed: J4.18 (DEBUG-1), TP12.1
unnamed: J4.19 (DEBUG-2), TP13.1
unnamed: J4.20 (DEBUG-3), TP14.1
unnamed: J4.16 (SWO), TP10.1
unnamed: J12.1, R34.2
unnamed: LS1.2, Q2.3 (D)
unnamed: Q2.1 (G), R25.1, TP37.1, U1.28 (PB15)
unnamed: Q3.3 (D), R34.1
unnamed: TP43.1, U1.38 (PA15)
unnamed: TP17.1, U1.20 (PB2)
unnamed: TP18.1, U1.39 (PB3)
unnamed: TP19.1, U1.45 (PB8)
unnamed: TP39.1, U1.46 (PB9)
unnamed: TP40.1, U1.25 (PB12)
unnamed: TP42.1, U1.26 (PB13)
unnamed: R24.1, U1.27 (PB14)
unnamed: TP21.1, U1.2 (PC13)
unnamed: TP22.1, U1.3 (PC14-OSC32_IN)
unnamed: TP23.1, U1.4 (PC15-OSC32_OUT)
unnamed: C16.1, U1.5 (PF0-OSC_IN), X1.3
unnamed: C17.1, U1.6 (PF1-OSC_OUT), X1.1
unnamed: R20.1, U4.2 (K)
unnamed: R22.1, U5.2 (K)
unnamed: R28.2, R39.1, U6.3 (+)
unnamed: R39.2, R40.1, U6.4 (-)
unnamed: R28.1, U8.32 (RNFS), U8.33 (RNF), U8.34 (RNF), U8.35 (RNF)
UMB_~ON: U1.29 (PA8); also elsewhere on the board
VBUS: C23.1, C24.1, C28.1, U8.24 (VCC), U8.25 (VCC), U8.26 (VCC); also elsewhere on the board

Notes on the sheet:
2nd sensor optional
Drive ~{PS} low to put in sleep mode (Low power and HI-Z outputs)
To DRV5056 PCBAs Analog Linear Hall Effect Sensors
Connector going to 3.5 mm jack serial port, such as TTL-232R-3V3-AJ or equivalent. 3.5 mm bulkhead mount jack is Schurter 4832.2300.
Deploy signals from Telemetrum flight computer
3.5mm Serial Jack
TODO: buzzer too quiet!
Motor: Pololu #3205 47:1 gear, 12V, 5A
Hall Effect Rotation Sensors
Board Address
PWM Control: IN1 IN2 OUT1 OUT2 L L HI-Z HI-Z L H GND VCC H L VCC GND H H GND GND
Note: Optoisolators populated only on interface board Hall effect sensors, motor driver, and indicators populated only on main, drogue, and ballute boards
Telemetrum Flight Computer Opto-isolated Inputs
Indicators
Debug Connector
MOTOR_ISENSE voltage = I * 0.033 * 20 + 0 Thus I = MOTOR_ISENSE / 0.66 (Max current is 3.3V / 0.66 = 5 A)
Addresses: AD1 AD0 Board 0 0 Interface 0 1 Ballute 1 0 Drogue Chute 1 1 Main Chute
Parachute Deployer Motor Driver
Telemetrum signals driven low when active, driving isolated signals high
Max current: MOTOR_ILIM = 3.3v => VREF = 1.65V. Imax = 1.65 / 3 / 0.099 = 5.6 A MOTOR_ILIM(V) Imax(A) 1.0 V 1.7 A 2.0 V 3.4 A 3.0 V 5.1 A
CAN Transceiver

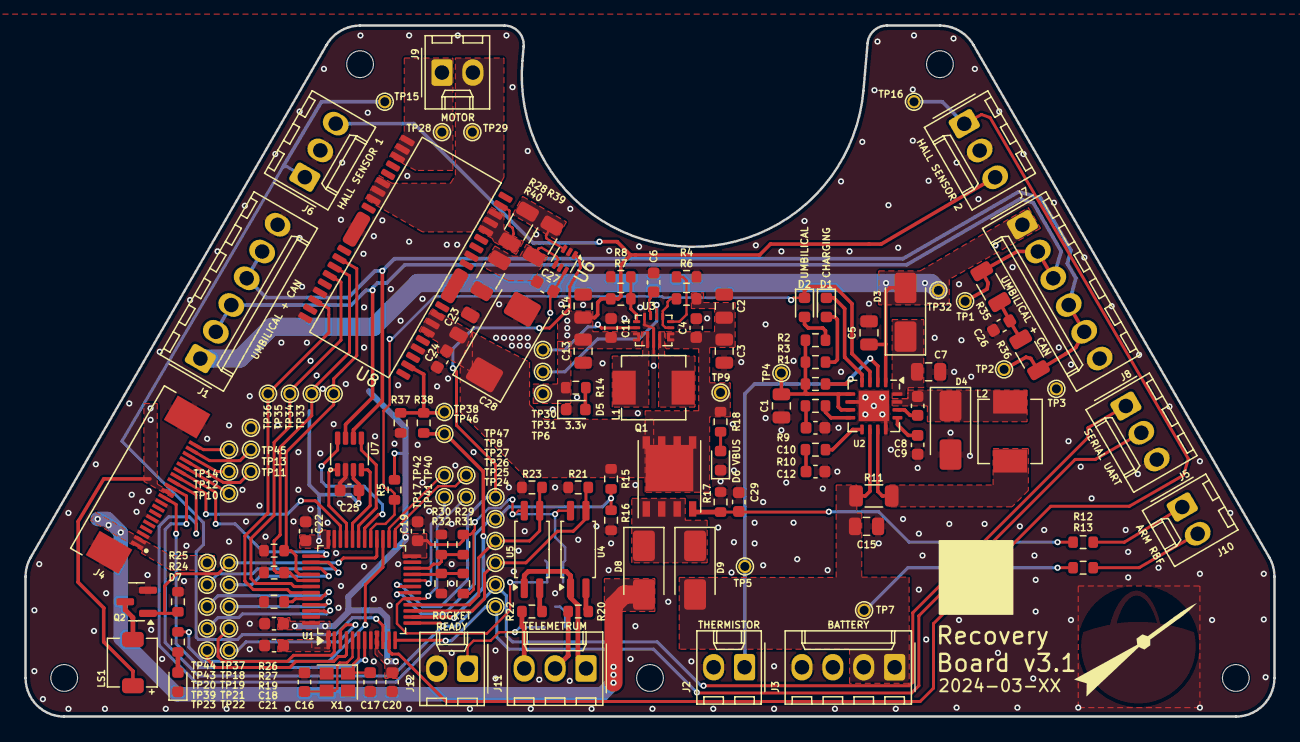
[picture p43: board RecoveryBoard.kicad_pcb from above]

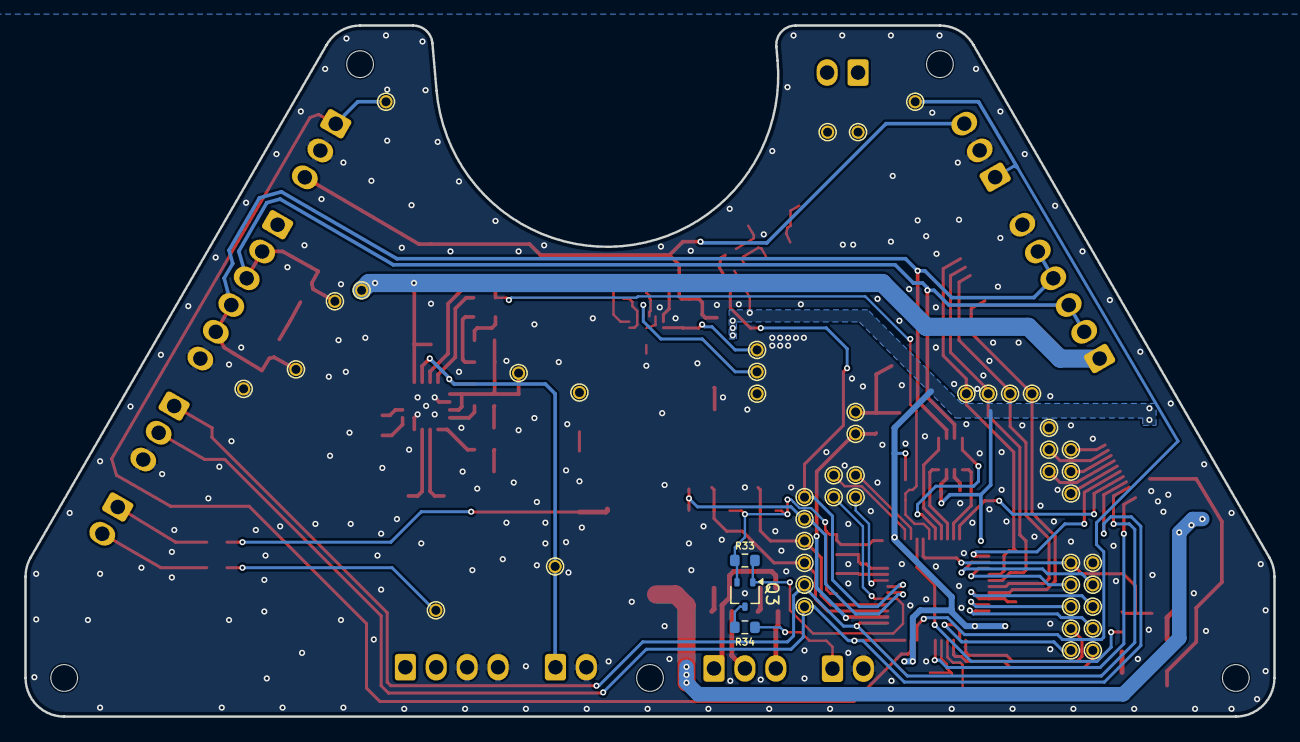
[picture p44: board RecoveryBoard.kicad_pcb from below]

Board: 2 copper layers, 102.7 x 56.8 mm, 153 parts (3 on the bottom side), 96 nets.

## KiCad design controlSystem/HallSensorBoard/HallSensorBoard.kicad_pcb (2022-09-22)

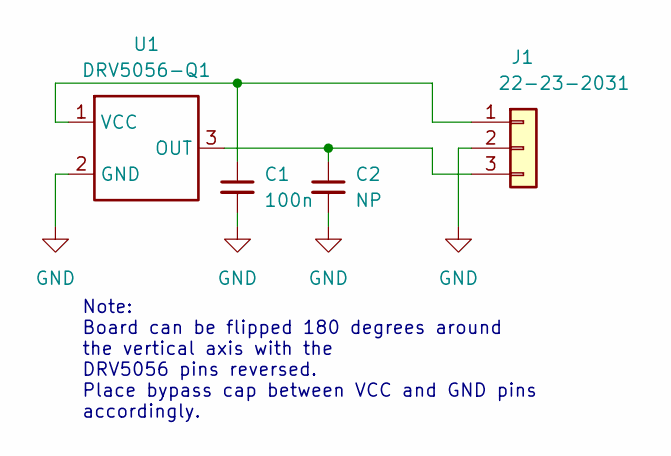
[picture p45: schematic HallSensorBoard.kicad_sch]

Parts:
C1: 100n; C_0603_1608Metric
C2: NP; C_0603_1608Metric
J1: 22-23-2031; U-TI-22-23-2031
U1: DRV5056-Q1; TO-92Flat

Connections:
GND: C1.2, C2.2, J1.2, U1.2 (GND)
unnamed: C1.1, J1.1, U1.1 (VCC)
unnamed: C2.1, J1.3, U1.3 (OUT)

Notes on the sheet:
Note: Board can be flipped 180 degrees around the vertical axis with the DRV5056 pins reversed. Place bypass cap between VCC and GND pins accordingly.

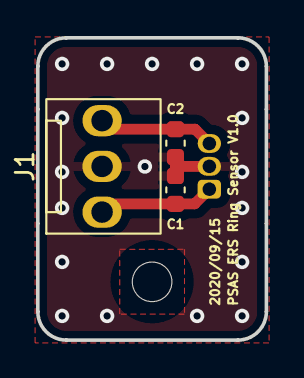
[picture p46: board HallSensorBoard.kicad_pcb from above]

Board: 2 copper layers, 12.7 x 16.8 mm, 4 parts (1 on the bottom side), 3 nets.

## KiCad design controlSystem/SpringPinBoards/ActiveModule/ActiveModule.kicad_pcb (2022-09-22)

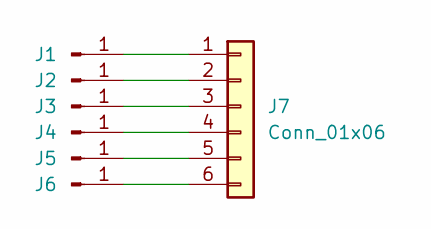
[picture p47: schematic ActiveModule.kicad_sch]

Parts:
J1, J2, J3, J4, J5, J6: Conn_01x01_Male; Mill-Max-0921-5-15-20-77-14-11-0
J7: Conn_01x06; PinHeader_1x06_P2.00mm_Vertical

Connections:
unnamed: J1.1, J7.1
unnamed: J2.1, J7.2
unnamed: J3.1, J7.3
unnamed: J4.1, J7.4
unnamed: J5.1, J7.5
unnamed: J6.1, J7.6

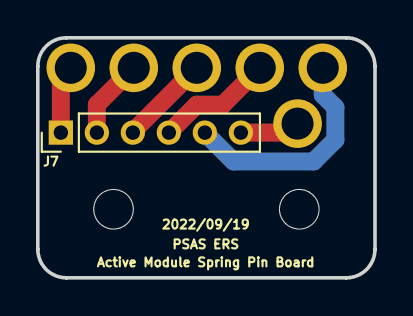
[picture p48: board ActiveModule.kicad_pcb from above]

Board: 2 copper layers, 18.7 x 13.3 mm, 7 parts (0 on the bottom side), 6 nets.

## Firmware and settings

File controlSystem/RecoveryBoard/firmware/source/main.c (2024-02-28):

/*
    ChibiOS - Copyright (C) 2006..2018 Giovanni Di Sirio

    Licensed under the Apache License, Version 2.0 (the "License");
    you may not use this file except in compliance with the License.
    You may obtain a copy of the License at

        http://www.apache.org/licenses/LICENSE-2.0

    Unless required by applicable law or agreed to in writing, software
    distributed under the License is distributed on an "AS IS" BASIS,
    WITHOUT WARRANTIES OR CONDITIONS OF ANY KIND, either express or implied.
    See the License for the specific language governing permissions and
    limitations under the License.
*/

// ChibiOS includes

#include "ch.h"
#include "hal.h"
#include "chprintf.h"
#include <string.h>
#include "shell.h"
#include "recovery.h"
#include "blinky.h"
//#include "telemetrum.h"
#include "mainchute.h"
#include "position.h"
#include "beep.h"


volatile enum recoverystatetype recoveryState = disarmed;
volatile enum PositionCommandtype PositionCommand = idle;
volatile enum mainchutecommandtype mainchuteCommand = idle_m;

//===========================================================================================
// Shell stuff
//===========================================================================================

static THD_WORKING_AREA(waShell, 1024);

void print_hall_sensors(void) {
	extern position_state_t g_position_state;
	chprintf(DEBUG_SD, "\r\nSensor 1: %d %s\r\n", g_position_state.sensor1, sensor_voltage_status_t_to_str(g_position_state.sensor1_voltage_status));
	chprintf(DEBUG_SD, "Sensor 2: %d %s\r\n", g_position_state.sensor2, sensor_voltage_status_t_to_str(g_position_state.sensor2_voltage_status));
	chprintf(DEBUG_SD, "Ring Position: %s\r\n", ring_position_t_to_str(g_position_state.ring_position));
}


static void cmd_state(BaseSequentialStream *chp, int argc, char *argv[]) {
	print_hall_sensors();

    /**/
    if (argc < 1) {
        switch(recoveryState) {
			case armed:
				chprintf(chp, "State = ARMED (valid commands: 'arm', 'disarm', and 'reset').\r\n");
				break;

			case disarmed:
				chprintf(chp, "State = DISARMED (valid commands: 'arm', 'disarm' and 'reset')\r\n");
				break; /* optional */

			default : /* Optional */
				chprintf(chp, "STATE = INVALID; SWITCHING TO ARMED\r\n");
				recoveryState = armed;
        }
        chThdSleepMilliseconds(10); // Wait for printout (100 char ~ 10 ms)
        return;
    }
    
    if (!strcmp(argv[0], "arm")) {
        recoveryState = armed;
        chprintf(chp, "STATE = ARMED\r\n");
    } else if (!strcmp(argv[0], "disarm")) {
        recoveryState = disarmed;
        chprintf(chp, "STATE = DISARMED\r\n");
    } else if (!strcmp(argv[0], "reset")) {
        NVIC_SystemReset();
    } else {
        chprintf(chp,"Usage: state <command>\r\n"
                     "    arm, disarm, and reset\r\n"
                     "\r\n");
    }
    chThdSleepMilliseconds(10); // Wait for printout (100 char ~ 10 ms)
}


static void cmd_lock(BaseSequentialStream *chp, int argc, char *argv[]) {
	drive_motor(true, 10, false);
}

static void cmd_unlock(BaseSequentialStream *chp, int argc, char *argv[]) {
	drive_motor(false, 10, false);
}


static void cmd_lock_full(BaseSequentialStream *chp, int argc, char *argv[]) {
	drive_motor(true, 10, true);
}

static void cmd_unlock_full(BaseSequentialStream *chp, int argc, char *argv[]) {
	drive_motor(false, 10, true);
}

static void cmd_stream(BaseSequentialStream *chp, int argc, char *argv[]) {
	for(;;) {
		print_hall_sensors();
		chThdSleepMilliseconds(1000);
	}
}

static void cmd_Position(BaseSequentialStream *chp, int argc, char *argv[]) {
	if (argc == 1) {
		if (!strcmp(argv[0], "lock")) {
			chprintf(chp, "Command: LOCKING ERS \r\n");
			PositionCommand = lock;
			return;
		}
		if (!strcmp(argv[0], "unlock")) {
			chprintf(chp, "Command: UNLOCKING ERS \r\n");
			PositionCommand = unlock;
			return;
		}
	}}

static void cmd_Beep(BaseSequentialStream *chp, int argc, char *argv[]) {
	(void)argc;
	(void)argv;
	chprintf(chp, "slayyyyy\r\n");
	beep();
}

    
static const ShellCommand commands[] = {
    {"state", cmd_state},
    {"pos", cmd_Position},
	{"u", cmd_unlock},//dev debug use only
	{"l", cmd_lock},//dev debug use only
	{"U", cmd_unlock_full},//dev debug use only
	{"L", cmd_lock_full},//dev debug use only
	{"stream", cmd_stream},
    {"beep", cmd_Beep},

    {NULL, NULL}
};

static const ShellConfig shell_cfg = {
    DEBUG_SD,
    commands
};


//===========================================================================================
// main
//===========================================================================================

int main(void) {
    /*
     * System initializations.
     * - HAL initialization, this also initializes the configured device drivers
     *   and performs the board-specific initializations.
     * - Kernel initialization, the main() function becomes a thread and the
     *   RTOS is active.
     */
    halInit();
    chSysInit();
    
    // Activate the serial driver 2 using the driver default configuration.
    sdStart(&SD2, NULL);
    
    // Print a nice message that we're alive and don't let the shell stomp on the message
    chprintf(DEBUG_SD, "\r\nPSAS ERS control board starting up\r\n");
    chThdSleepMilliseconds(10); // Wait for printout (100 char ~ 10 ms)
    
    palSetLine(LINE_BATTREAD); //BATT_READ (shore power)

    beep_init();
    beep();

    // START THEM THREADS
    chThdCreateStatic(waBlinkyThread, sizeof(waBlinkyThread), NORMALPRIO, BlinkyThread, NULL);

    //chThdCreateStatic(waTelemetrumThread, sizeof(waTelemetrumThread), NORMALPRIO, TelemetrumThread, NULL);
   // chThdCreateStatic(waDrogueThread, sizeof(waDrogueThread), NORMALPRIO, DrogueThread, NULL);
    chThdCreateStatic(waMainchuteThread, sizeof(waMainchuteThread), NORMALPRIO, MainchuteThread, NULL);    
    chThdCreateStatic(waShell, sizeof(waShell), NORMALPRIO, shellThread, (void *)&shell_cfg);
    chThdCreateStatic(waPositionThread, sizeof(waPositionThread), NORMALPRIO, PositionThread, NULL);
    
    
    while (true) {
        chThdSleepMilliseconds(500);
    }
}

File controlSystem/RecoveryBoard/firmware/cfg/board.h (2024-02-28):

/*
    ChibiOS - Copyright (C) 2006..2020 Giovanni Di Sirio

    Licensed under the Apache License, Version 2.0 (the "License");
    you may not use this file except in compliance with the License.
    You may obtain a copy of the License at

        http://www.apache.org/licenses/LICENSE-2.0

    Unless required by applicable law or agreed to in writing, software
    distributed under the License is distributed on an "AS IS" BASIS,
    WITHOUT WARRANTIES OR CONDITIONS OF ANY KIND, either express or implied.
    See the License for the specific language governing permissions and
    limitations under the License.
*/

/*
 * This file has been automatically generated using ChibiStudio board
 * generator plugin. Do not edit manually.
 */

#ifndef BOARD_H
#define BOARD_H

/*===========================================================================*/
/* Driver constants.                                                         */
/*===========================================================================*/

/*
 * Setup for STMicroelectronics STM32 Nucleo64-F091RC board.
 */

/*
 * Board identifier.
 */
#define BOARD_ST_NUCLEO64_F091RC
#define BOARD_NAME                  "STMicroelectronics STM32 Nucleo64-F091RC"

/*
 * Board oscillators-related settings.
 * NOTE: LSE not fitted.
 */
#if !defined(STM32_LSECLK)
#define STM32_LSECLK                0U
#endif

#define STM32_LSEDRV                (3U << 3U)

#if !defined(STM32_HSECLK)
#define STM32_HSECLK                16000000U
#endif



/*
 * MCU type as defined in the ST header.
 */
#define STM32F091xC

/*
 * IO pins assignments.
 */
#define GPIOA_HALL1                0U
#define GPIOA_HALL2                1U
#define GPIOA_USART2_TX            2U
#define GPIOA_USART2_RX            3U
#define GPIOA_MOTOR_ILIM           4U
#define GPIOA_ISO_DROGUE           5U
#define GPIOA_ISO_MAIN             6U
#define GPIOA_N_ROCKET_READY       7U
#define GPIOA_N_UMB_ON             8U
#define GPIOA_CAN_SILENT           9U
#define GPIOA_CAN_SHDN             10U
#define GPIOA_PIN11                11U
#define GPIOA_PIN12                12U
#define GPIOA_SWDIO                13U
#define GPIOA_SWCLK                14U
#define GPIOA_UNUSEDPA15           15U

#define GPIOB_BATTREAD              0U
#define GPIOB_MOTOR_ISENSE          1U
#define GPIOB_UNUSEDPB2             2U
#define GPIOB_SWO                   3U
#define GPIOB_DEPLOY1               4U
#define GPIOB_DEPLOY2               5U
#define GPIOB_N_MOTOR_PS            6U
#define GPIOB_N_MOTOR_FAIL_A        7U
#define GPIOB_UNUSEDPB8             8U
#define GPIOB_UNUSEDPB9             9U
#define GPIOB_AD0                   10U
#define GPIOB_AD1                   11U
#define GPIOB_UNUSEDPB12            12U
#define GPIOB_UNUSEDPB13            13U
#define GPIOB_LED                   14U
#define GPIOB_SPEAKER               15U

#define GPIOC_ARD_A5                0U
#define GPIOC_ARD_A4                1U
#define GPIOC_PIN2                  2U
#define GPIOC_PIN3                  3U
#define GPIOC_PIN4                  4U
#define GPIOC_PIN5                  5U
#define GPIOC_PIN6                  6U
#define GPIOC_ARD_D9                7U
#define GPIOC_PIN8                  8U
#define GPIOC_PIN9                  9U
#define GPIOC_PIN10                 10U
#define GPIOC_PIN11                 11U
#define GPIOC_PIN12                 12U
#define GPIOC_TP_PC13               13U
#define GPIOC_TP_PC14               14U
#define GPIOC_TP_PC15               15U

#define GPIOD_PIN0                  0U
#define GPIOD_PIN1                  1U
#define GPIOD_PIN2                  2U
#define GPIOD_PIN3                  3U
#define GPIOD_PIN4                  4U
#define GPIOD_PIN5                  5U
#define GPIOD_PIN6                  6U
#define GPIOD_PIN7                  7U
#define GPIOD_PIN8                  8U
#define GPIOD_PIN9                  9U
#define GPIOD_PIN10                 10U
#define GPIOD_PIN11                 11U
#define GPIOD_PIN12                 12U
#define GPIOD_PIN13                 13U
#define GPIOD_PIN14                 14U
#define GPIOD_PIN15                 15U

#define GPIOE_PIN0                  0U
#define GPIOE_PIN1                  1U
#define GPIOE_PIN2                  2U
#define GPIOE_PIN3                  3U
#define GPIOE_PIN4                  4U
#define GPIOE_PIN5                  5U
#define GPIOE_PIN6                  6U
#define GPIOE_PIN7                  7U
#define GPIOE_PIN8                  8U
#define GPIOE_PIN9                  9U
#define GPIOE_PIN10                 10U
#define GPIOE_PIN11                 11U
#define GPIOE_PIN12                 12U
#define GPIOE_PIN13                 13U
#define GPIOE_PIN14                 14U
#define GPIOE_PIN15                 15U
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

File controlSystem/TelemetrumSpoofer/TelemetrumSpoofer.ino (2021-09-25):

// telespoof.ino -- PSAS LV3.1 Recovery
// author: Sean Lai
//
// Spoofs telemetrum signals to deploy main and drogue parachutes
// after receiving a GO signal. For the drop test, GO signal is a
// an opened circuit.
// Usage: drogue_delay --> time from GO to drogue deployment
//        main_delay   --> time from GO to main   deployment
//        Set these to values as defined by flight model.
//        IMPORTANT: The code expects these values in milliseconds
//
// Physical setup:
// -- connect jumper to short (with static line) to armed_pin and GND
// -- connect drogue_pin and main_pin to control board as required

// Setup pin numbers
const int armed_pin = 8;
const int drogue_pin = 9;
const int main_pin = 10;

// debugging pins
// const int drogue_read_pin = 11;
// const int main_read_pin = 12;

void setup() {
    // configure pins
    pinMode(armed_pin, INPUT_PULLUP); // Arming input to ground via a static line: High = armed, Low = safed
    pinMode(drogue_pin, INPUT);       // Yes, it's an output, but low = fire and we'll let it float when not firing
    pinMode(main_pin, INPUT);         // Yes, it's an output, but low = fire and we'll let it float when not firing

    // Serial comms for debugging
    Serial.begin(9600);
}

void loop() {
    // Set these as defined by flight model. Values in milliseconds
    const int drogue_delay = 1500;
    const int main_delay = 6000;

    // Setup state variables
    static int GO_time = 0;
    static int arm_debounce = 0;
    static bool armed = false;
    static bool drogue = false;
    static bool main = false;

    //---------------- Serial debugging ----------------
    // Serial.println(digitalRead(armed_pin));
    // Serial.print("armed = ");
    // Serial.print(armed);
    // Serial.print("  |  drogue deployed = ");
    // Serial.print(drogue);
    // Serial.print("  |  drogue reading = ");
    // Serial.print(digitalRead(drogue_read_pin));
    // Serial.print("  |  main deployed = ");
    // Serial.print(main);
    // Serial.print("  |  main reading = ");
    // Serial.println(digitalRead(main_read_pin));

    // Debounce the arm_pin; it must be unshorted to ground for 100 ms
    // else the count resets. Once we pass 100 ms, we fire the system.
    if (armed == false) {
          if (digitalRead(armed_pin) == 1) {
            ++arm_debounce;
            if (arm_debounce > 9) {
                GO_time = millis();
                armed = true;          
            }
            else {
                arm_debounce = 0;
            }
        }
    }
    else {
        if (millis()-GO_time > drogue_delay) {
            // Send signal to release drogue chute
            pinMode(drogue_pin, OUTPUT);
            digitalWrite(drogue_pin, 0);
            drogue = true;
        }
        if (millis()-GO_time > main_delay) {
            // Send signal to release main chute
            pinMode(main_pin, OUTPUT);
            digitalWrite(main_pin, 0);
            main = true;
        } 
    }

    // Set the time to be >= 10 ms
    delay (10);
}
id|moose>
  

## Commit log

2019-02-17 Uploading CAD files and Surgical Tubing Pull Test
    [Alignment_Pins.SLDPRT, Assem1.SLDASM, Assem1.SLDPRT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]
2019-02-17 Created Assembly for 2nd Concept, deleted files non needed
    [Assem1.SLDASM, Assem1.SLDPRT, Bearing_RMA.SLDPRT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]
2019-02-17 Updated assembly with motor based on old eNSR
    [Complete_Assembly.SLDASM, Concept_Assem_2.SLDASM, Lower_Ring.SLDPRT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]
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2019-02-26 adding CAD files mainly for 3 ring release design
    [3-ring_assy.SLDASM, 3-ring_dimensions.SLDDRW, 3-ring_ratio.SLDDRW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]
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2019-03-17 Worked on system architecture assembly for Base 11 report
    [2994T410_FORGED STL HOIST RING FOR LIFTING.SLDPRT, 2994T630_FORGED STL HOIST RING FOR LIFTING.SLDPRT, 3-ring_assy.SLDASM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]
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2019-04-02 Made changes to bottom ring and ST ring
    [Base11_NCSR.SLDASM, Bottom_ring.SLDPRT, Cup_Chute_Drogue^eNSR_v2.2.SLDPRT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]
2019-04-04 Mainly changes to the 3-ring CAD, little bit of change within the NCSR assembly
    [3-ring_assy.SLDASM, Base11_NCSR.SLDASM, Current_NCSR.SLDASM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]
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2019-04-04 Making sure any new CAD updates are pushed
    [Bottom_ring.SLDDRW, Bottom_ring.SLDPRT, Bottom_ring.STEP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]
2019-04-05 added drawings and part edits per machine shop request
    [Bottom_ring.SLDDRW, Bottom_ring.SLDPRT, Top_ring.SLDDRW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]
2019-04-05 Modeled the BLDC motor, modified the motor mounting bracket and updated assemblies
    [BLDC_Gear_Motor_100rpm.SLDPRT, Current_NCSR.SLDASM, motor base plate assembly.SLDASM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]
2019-04-05 Changed bottom ring and ST ring to be two parts again. This MUST happen so that the parts may be machined!
    [Base11_NCSR.SLDASM, Bottom_ring_2.SLDPRT, Bottom_ring_assy.SLDASM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]
2019-04-05 Made bottom ring and ST ring separate parts again. This is needed for machining.
    [Sys_architecture.SLDASM]
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2019-04-12 Added pizza table and files for testing DCR
    [3-ring_dimensions.SLDDRW, NCS_V3.SLDASM, Sys_architecture.SLDASM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]
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2019-04-14 motor mnt design, pizza table design, 3 ring design edits
    [2949T380_316 SS HOIST RING FOR LIFTING.SLDPRT, 3-ring_assy.1.SLDASM, 3-ring_assy.SLDASM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]
2019-04-16 Added radii to nubs due to interference
    [NCS_V3.SLDASM, keeper_assy_V3.SLDASM, motor_assy.SLDASM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]
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2019-08-06 added parachute cups v3.0 & PIZZA Table v4
    [Assem3.2.SLDASM, Assem_Parachute_Cups.SLDASM, Cup_Chute_Drogue^ERS_v3.0.SLDPRT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]
2019-09-17 Updated twist coupling to tighten up system
    [twist_coupling_V4.SLDPRT]
2019-09-17 Added drawing to submit to WPP for new twist coupling
    [twist_coupling_V3.SLDDRW, twist_coupling_V4.SLDDRW]
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2019-11-09 added skirt to twist coupleing for machining and standoff legs for pizza table
    [standoff_nomount.SLDPRT, standoff_withmount.SLDPRT, twist_coupling_V3_skirt.SLDPRT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]
2019-11-11 fixed drawing files, added step files, removed standoffs w/o mount
    [7880K450_HT-LOAD MTL GEAR--20 DEG PRESSURE ANGLE.SLDPRT, standoff_withmount.SLDDRW, standoff_withmount.SLDPRT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]
2019-11-19 Designed new motor housing, added revised spacer ring, organized parts to be machined and 3d printed
    [94414A108_ALLOY STL TORX DRIVE FLAT-HEAD SCKT CAP SCREW.SLDPRT, LinAct_Bracket_Back.SLDPRT, LinAct_Bracket_Back.STEP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]
2019-12-06 Remade pizza table, modified motor mount, craeted circuit board mock up an drawing, modified new motor gear and drawing
    [2662N400_PLASTIC GEAR - 20 DEGREE PRESSURE ANGLE.SLDPRT, 3-ring_assy_V1.SLDASM, 7880K450_HT-LOAD MTL GEAR--20 DEG PRESSURE ANGLE.SLDPRT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]
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2019-12-07 updated linear actuator bracket, added STL files for Adam to print in ../cad/formachining/STLfiles
    [Assem3.2rev1.SLDASM, LinAct_Bracket_Back.SLDPRT, LinAct_Bracket_Back_rev1.SLDPRT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]
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2020-01-15 OCD moving around to put things in the right places and right names.
    [RecoveryBoard-BOM.xlsx, RecoveryBoard.brd, RecoveryBoard.sch]
2020-01-15 OCD on package sizes 0603 for normal caps and resistors; 0805 for large caps, and larger yet for larger caps.
    [RecoveryBoard.brd, RecoveryBoard.sch]
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2020-01-16 More destruction on Ben's nice board. Good job Ben for putting up with Andrew.
    [RecoveryBoard.brd, RecoveryBoard.sch]
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2020-01-31 Layout cleanup of RecoveryBoard for manufacturing. Sent off to Fab as v1.0
    [RecoveryBoard.brd, RecoveryBoard.sch]
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2020-02-05 Updated BOM with Ben to fix a few parts.
    [RecoveryBoard-BOM.xlsx]
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2020-03-12 fixed first round of issues with Rev1.0, and fixed some libraries as well
    [RecoveryBoard.brd, RecoveryBoard.sch]
2020-03-14 updated board with more test points, rearranged LA pins, and rearannged AI STM32 pins
    [RecoveryBoard.brd, RecoveryBoard.sch]
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2020-04-05 nearly done with mission analysis, still working on documentation while waiting for a definitive test site
    [early_across_data.csv, early_against_data.csv, nodrogue_across_data.csv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]
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2021-05-19 Started over from scratch using NUCLEO32-F042 demo project. Something in the previous code was killing the ability to reset the STM32F042 which made it *program once and never again* without doing we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
    [oocd.cfg]
2021-05-19 Updated board.h with recovery board pinouts; fixed problem? Maybe?
    [board.h, main.c]
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2021-05-19 First big checkpoint of recovery-firmware: STM32 is using HSE crystal, serial port, and tools seem to be working correctly. Committing new schematic and board file with updated names, but no electric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
    [RecoveryBoard.brd, RecoveryBoard.sch]
2021-05-21 Fixed shell, now works!
    [main.c]
2021-05-23 Spun off blinky to a separate file, added shell commands, added polling for telemetrum signals, and updated board file with better names for signals (no changes to layout or schematic).
    [RecoveryBoard.brd, RecoveryBoard.sch]
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2021-06-10 It works! It works! Had the motor reversed, and fixed a couple of motor movement ugs.
2021-06-15 Fixed a bug on firing the main. Then added commands to pulse the twist coupler clockwise or counter clockwise. Then added a command to rotate the twist coupler to the unlocked position.
    [main.c]
2021-06-15 Added Q7, which was missing from the BOM.
    [RecoveryBoard-BOM.xlsx]
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2021-08-31 Fixed sizing of slot in main cup
    [mainCup.SLDPRT, recoverySystem.SLDASM]
2021-09-13 Removed older CubeMX based firmware now that the ChibiOS-based one is feature equivalent (or more), and changed name to make Joe happy.
    [Learning Debug.cfg, PWM Capture Troubleshooting.xlsx, oocd.cfg]
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2023-01-03 Removes ERS v3 information and board which were never flown. Added ERS v4 readme to point to documentation.
    [RecoveryBoard-BOM.xlsx, RecoveryBoard.brd, RecoveryBoard.sch]
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2024-02-23 Fix typos in beep
    I uh, renamed a couple things and committed the grave sin of not
    compiling before committing. This should fix that.
    [beep.c]
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2024-02-28 v3.1. Cap to deal with spikes on RBF, 100k on main Q pull down, better notes on schematic for part numbers, moved Vbatt pickoff to after main Q.
    [RecoveryBoard.kicad_pcb, RecoveryBoard.kicad_sch, RecoveryBoardMicrocontroller.kicad_sch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]
2024-12-04 Stuffing four more v3.0 PCBs and discovered everything wasn't updated. Fixed BOM, fixed a lot of schematic errors especially in symbols, fixed some footprint errors, synchronized schematic and pcb, a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
    [RecoveryBoard.kicad_pcb, RecoveryBoard.kicad_sch, RecoveryBoard.xlsx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]
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2025-08-19 Setup CAN, PWM Drivers. Create Buzzer, CAN Tasks
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
